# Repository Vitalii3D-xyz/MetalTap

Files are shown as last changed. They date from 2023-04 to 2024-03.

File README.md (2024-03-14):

# MetalTap aka CNC Voron Tap
Drop in replacement for original Voron Tap designed especially for CNC milling. Works with all the same parts as original version.

# Where to buy
- **Worldwide Etsy Shop**: https://www.etsy.com/listing/1446827040/metal-tap-for-voron-cnc-voron-tap
- **EU lab4450**: https://lab4450.com/product/voron-cnc-tap-by-vitalii/
- **EU 3dptronics**: https://www.3dptronics.com/electronics/80-voron-cnc-tap-kit-by-vitalii.html

example of work

# BOM
- 8 BHCS M3x4
- 8 BHCS M3x6
- 1 BHCS M3x10
- 2 FHCS M3x4
- 2 6x3mm N52 disc magnet, get N52m or N52s if you plan to print in high temperature chamber as neodymium will loose magnetism forever after 80C
- 7 Mx3x4x5 heat insert

# Support for other optical sensors
[yonkimen](https://github.com/yonkiman) adapter for inexpensive optical endstop

Sensor: https://www.amazon.com/gp/product/B07MFT8NWJ?th=1

Model: https://www.printables.com/model/803495-modified-opto-mount-for-vitalii-tap/

img_0630 copy

## Assembling Instructions For Kit
[Assembling Instructions](https://www.youtube.com/watch?v=gwPNVVCuMag)

## How to attach belts
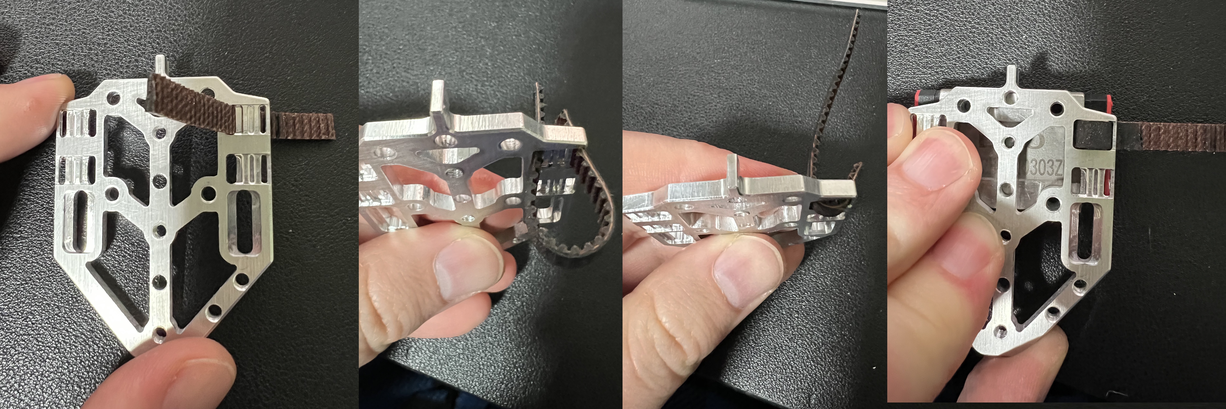
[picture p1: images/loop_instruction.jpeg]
Belts


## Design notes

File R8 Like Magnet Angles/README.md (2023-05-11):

I have tested this version myself, but results are not as good as original version. My Voron 2.4 350 may not be the best machine to test that so leaving to community to test.
# Instrunctions
- Print with Voron parts settings (optional: use Arachne for better letters visibility)
- Insert heat inserts, but make sure that surface is as flat as possible, use sandpaper or exacto knife to remove any
- Parts have L and R letters so attach them accordingly

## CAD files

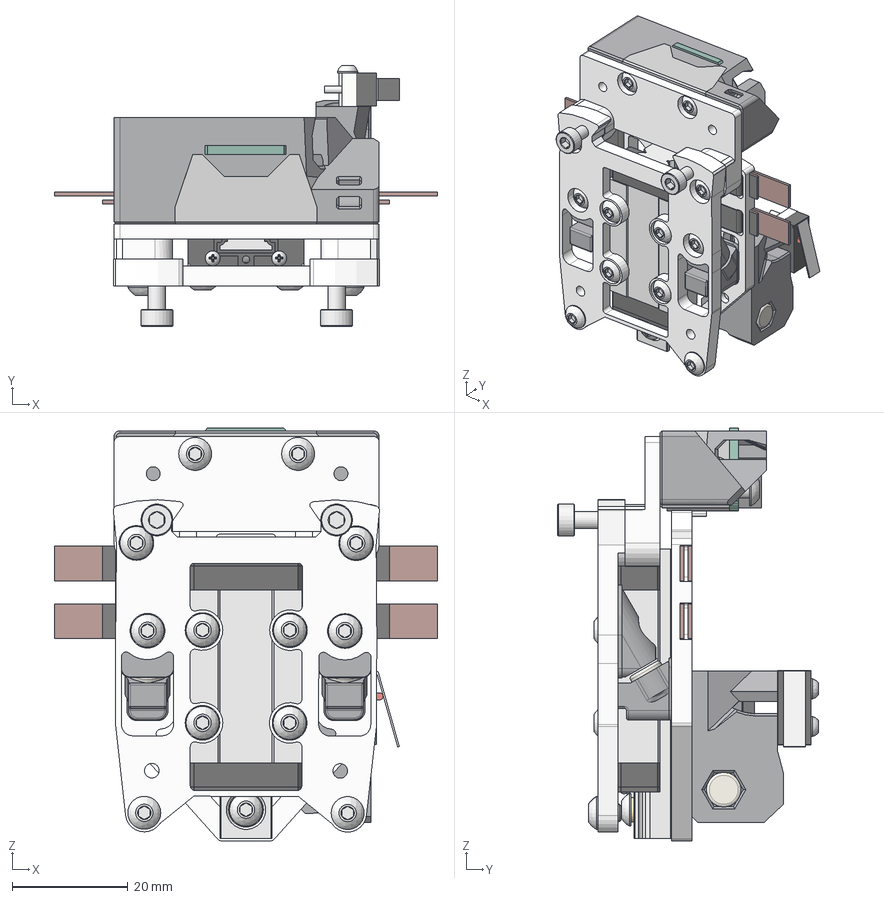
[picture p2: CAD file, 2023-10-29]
CAD/Metal Tap Assembly.step
66.1 x 45.1 x 71.3 mm
MGN9H Carriage
M3x4 BHCS x 8
M3x12 SHCS x 2
M3x6 BHCS x 10
M3x4 FHCS x 2
M3 5x4 Heatset Insert x 7
Carriage Front Screw Holder_1 x 2
6x3mm Magnet x 3
Carriage Center Magnet Holder_1 x 2
M2x10 Self-Tapping Screw x 2
Gates GT2 6mm Belt x 4
OPB990P51Z Optical Sensor
M3x8 BHCS
OptoTap PCB Mount
OptoTap PCB Dummy (1)

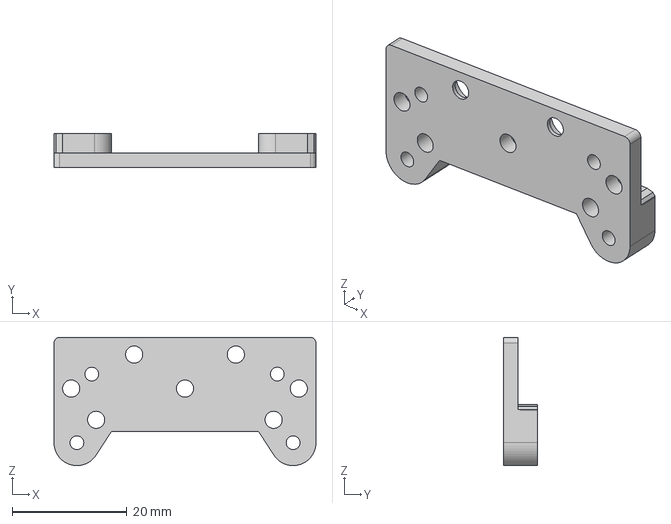
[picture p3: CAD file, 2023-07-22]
CAD/Aluminium Parts/Top Part.step
45.8 x 6.00 x 22.4 mm

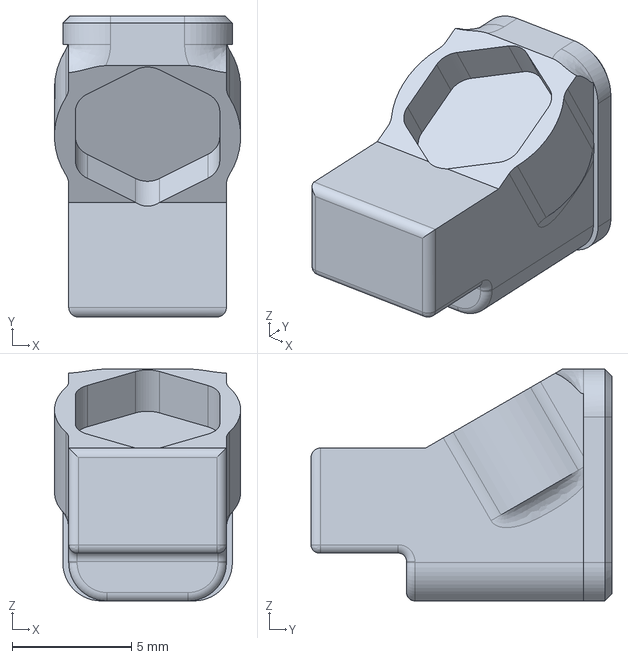
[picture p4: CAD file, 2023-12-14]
CAD/Printed Parts/Carriage Center Magnet Holder.step
7.79 x 12.6 x 9.70 mm

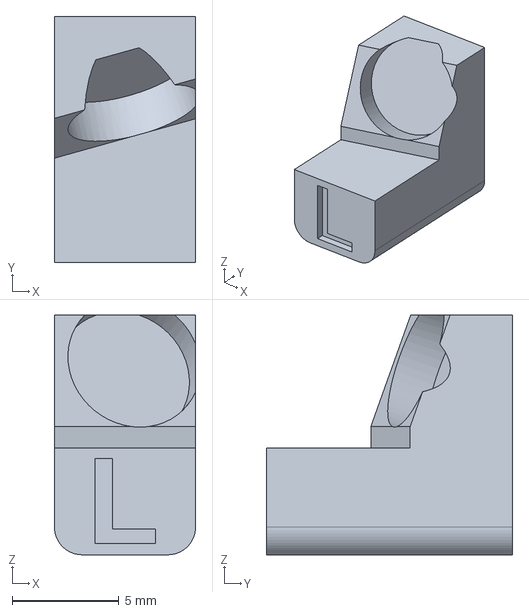
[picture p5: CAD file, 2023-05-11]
R8 Like Magnet Angles/CAD/Carriage Center Magnet Holder L.step
6.60 x 11.5 x 11.2 mm

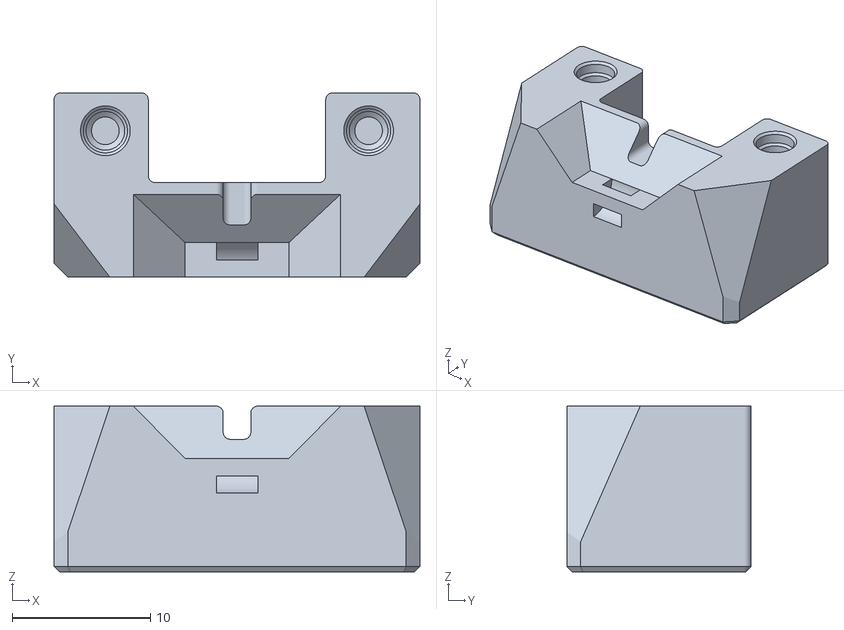
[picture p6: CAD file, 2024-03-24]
STLs/OptoTap_PCB_Mount.stl
26.5 x 13.4 x 12.0

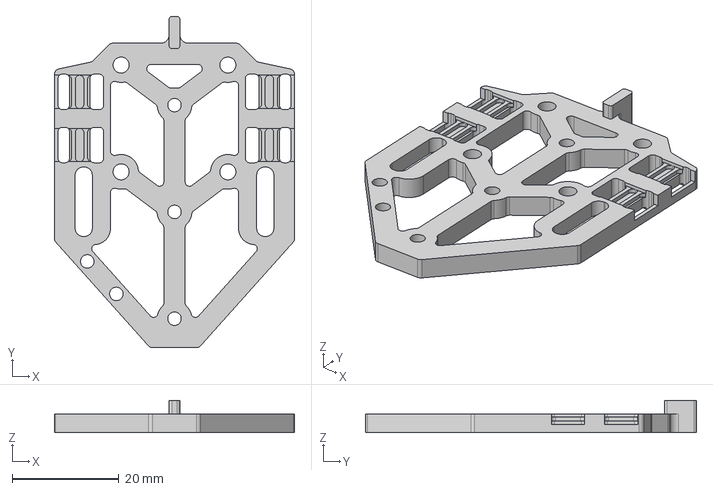
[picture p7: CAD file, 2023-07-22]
CAD/Aluminium Parts/Center Part.step
45.0 x 62.0 x 6.00 mm

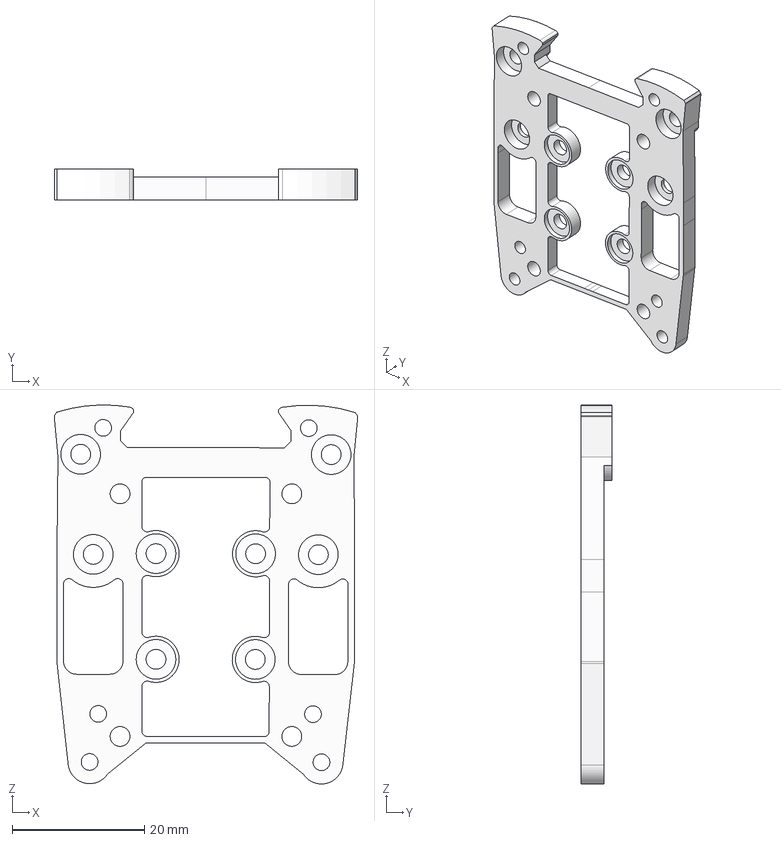
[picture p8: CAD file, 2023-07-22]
CAD/Aluminium Parts/Front Part.step
45.9 x 4.70 x 57.4 mm

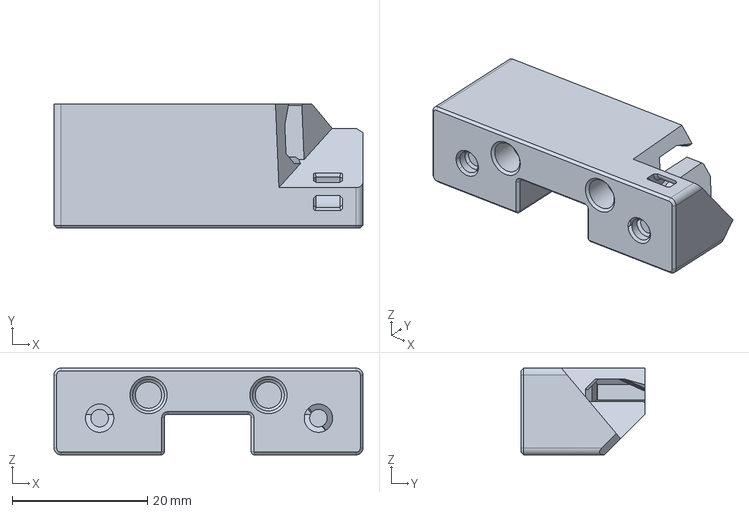
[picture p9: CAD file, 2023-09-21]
CAD/Printed Parts/Wired Optical Sensor Mount.step
45.8 x 18.4 x 12.9 mm

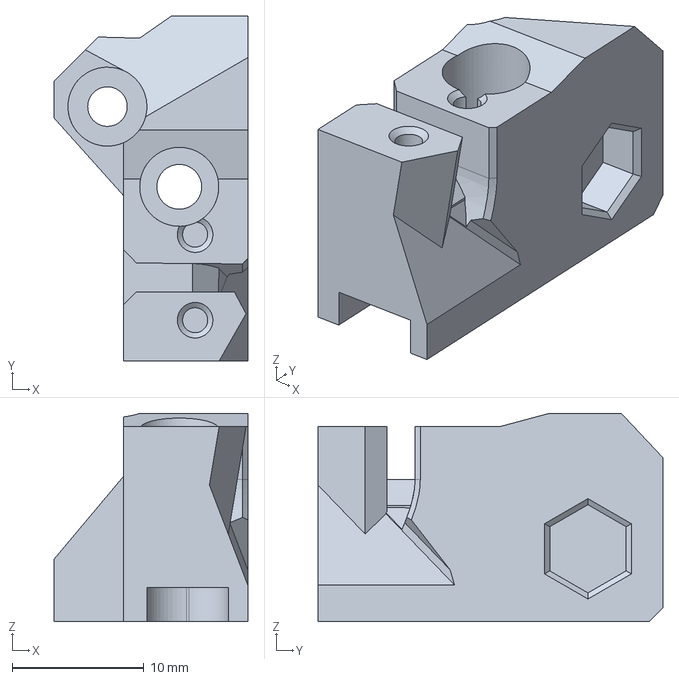
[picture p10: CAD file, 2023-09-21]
CAD/Printed Parts/X Endstop Holder.step
14.7 x 26.2 x 15.8 mm

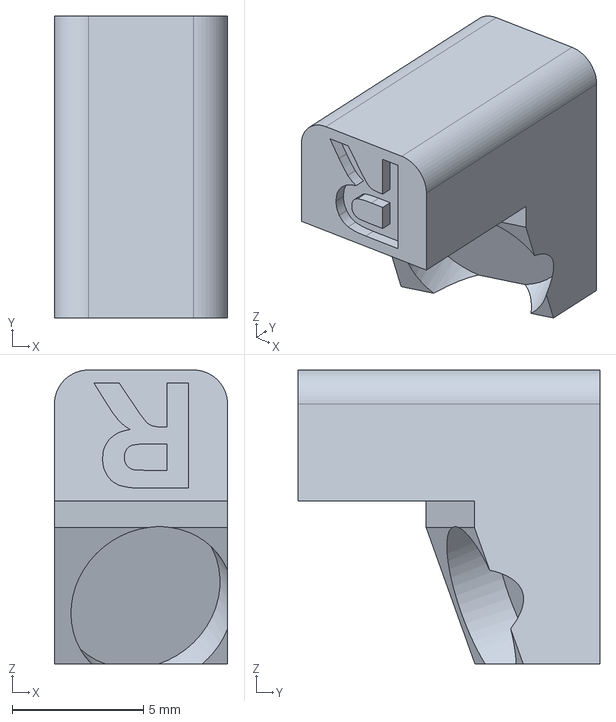
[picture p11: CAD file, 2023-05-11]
R8 Like Magnet Angles/CAD/Carriage Center Magnet Holder R.step
6.60 x 11.5 x 11.2 mm

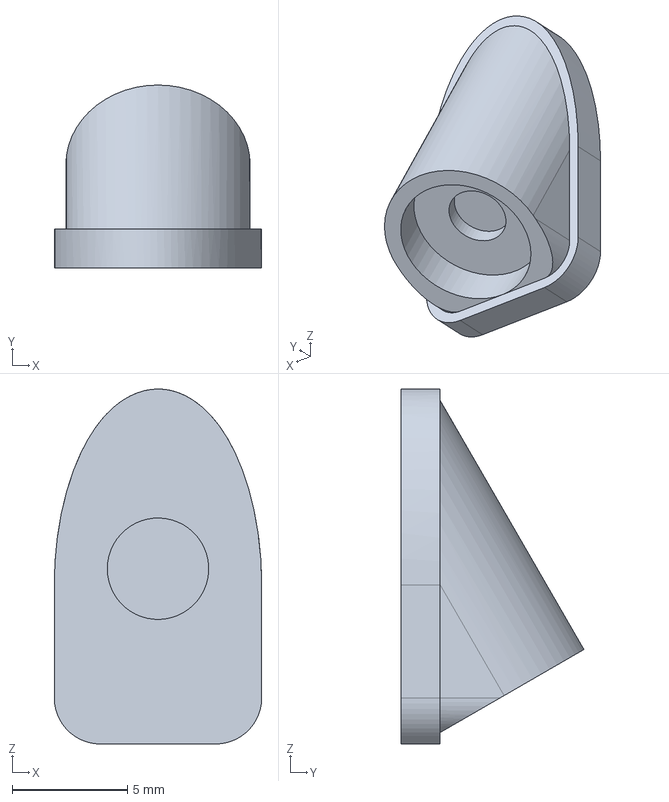
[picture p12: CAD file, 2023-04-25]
CAD/Printed Parts/Carriage Front Magnet Holder.step
9.00 x 7.94 x 15.4 mm

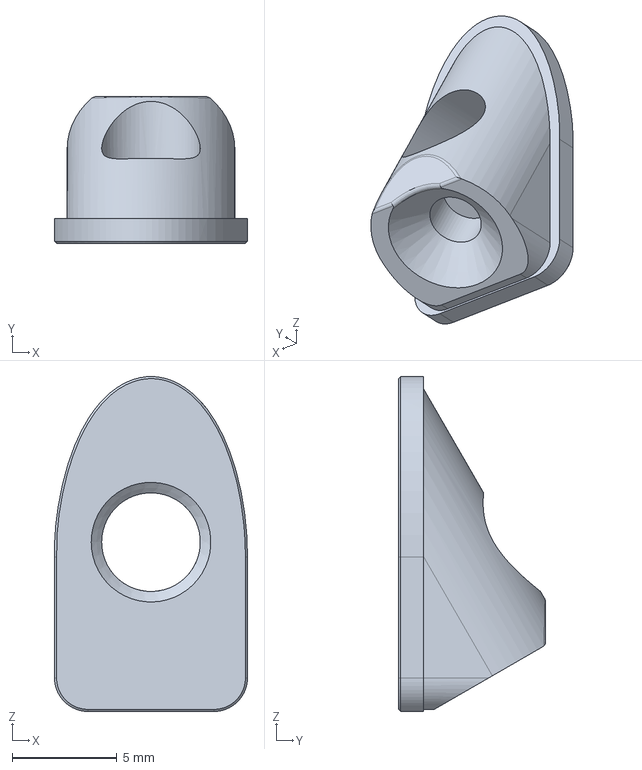
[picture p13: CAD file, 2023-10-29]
CAD/Printed Parts/Carriage Front Screw Holder.step
9.20 x 7.00 x 16.0 mm

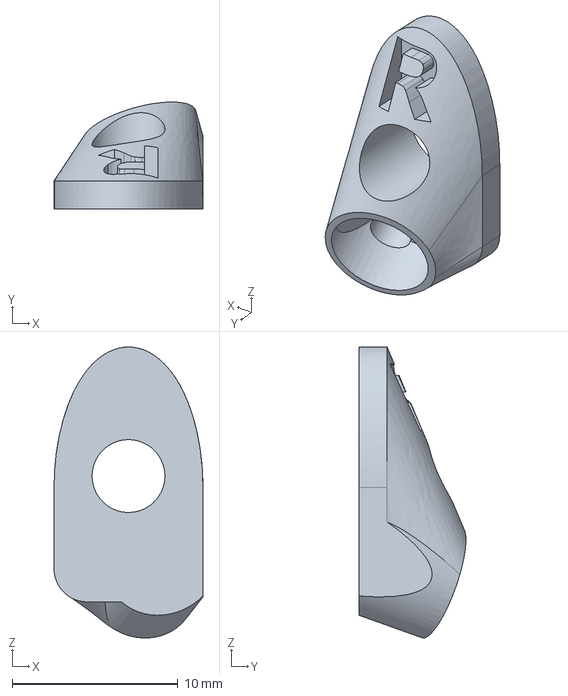
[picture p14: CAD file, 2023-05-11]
R8 Like Magnet Angles/CAD/Carriage Front Bolt Holder R.step
9.00 x 6.46 x 17.6 mm

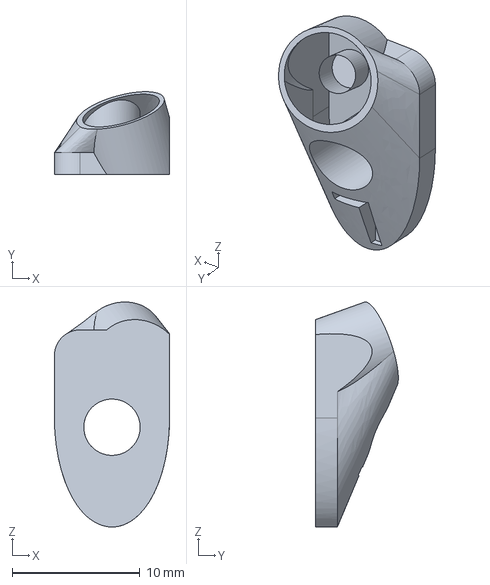
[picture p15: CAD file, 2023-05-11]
R8 Like Magnet Angles/CAD/Carriage Front Bolt Holder L.step
9.00 x 6.46 x 17.6 mm

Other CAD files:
STLs/Carriage Center Magnet Holder x2.stl
STLs/Wired Optical Sensor Mount.stl
STLs/X Endstop Holder.stl
STLs/Carriage Front Magnet Holder x2.stl
R8 Like Magnet Angles/STLs/Carriage Center Magnet Holder L.stl
R8 Like Magnet Angles/STLs/Carriage Center Magnet Holder R.stl
R8 Like Magnet Angles/STLs/Carriage Front Bolt Holder L.stl
R8 Like Magnet Angles/STLs/Carriage Front Bolt Holder R.stl
STLs/Carriage Front Screw Holder x2.stl

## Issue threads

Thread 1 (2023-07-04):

GPL issue? No CAD?

rogerlz, 2023-07-04:
Hey!

I am reaching out regarding the Voron-TAP project and its derivative work in your repository.

As Voron-TAP is released under the GPL (GNU General Public License), it is necessary to publish modifications. However, I could not find the CAD files in your repository. Would you please clarify this matter?

Thanks

Vitalii3D-xyz, 2023-07-05:
Hello rogerlz,

Thanks for the clarification inquiry. This project is indeed compatible with Voron TAP, but it is not derived from it in any shape or form and thus is not required to follow the GNU GPL licensing model.

Saying that I am still planning to release original design into open source community, but so far still looking into the best way of doing that.

samwiseg0, 2023-07-08:
As I can see where you have more than likely made the CAD yourself. The design that you are deriving your CAD from is using GPL thus you need to release your original source files as per the license.

Considering you are using the word "TAP" in your products name that alone supports the case that you used the original work to derive your version. Anyone looking at this product and the original can clearly see that they are _extremely_ similar. Furthermore, you even mention providing printed parts that have the same R8 magnet angles.  Which clearly means you are deriving your design from measurements you have taken from the original work.

Myself and members of the community encourage you to do the right thing in this case and release the files as per the license.

Vitalii3D-xyz, 2023-07-08:
Thanks for feedback @samwiseg0, I am not trying to disagree with you, but would like to understand better what "deriving your CAD from" means in your context. To make my own conclusion I have read GPL 3 again and while it is hard to apply it to CAD (as it was written for software development and operates with different entities) I can see some analogies.
According to GPL 3 derived work is using part of original source in new product, expanding original source or modifying original source. Another very important part is distribution of code.
Good shorter version with examples is available here: https://courses.cs.washington.edu/courses/cse490t/11sp/docs/DerivativeWorksGPL.pdf

Have I used original source in my design or have I modified original source: No
Do I distribute parts of original source: No

I would really like to understand how GPL 3 applies here.
> Considering you are using the word "TAP" in your products name
Is using word TAP automatically makes my work "deriving"? The same for questions about magnets angles. And just in case there are conversation in public Voron discord channel where Olof asks me about R8 angles and gives exact numbers.

samwiseg0, 2023-07-08:
> Have I used original source in my design or have I modified original source: No

I believe this is where the disconnect may be. Even though the original file itself is not being used does not mean that this is not a durative work. Creating your own CAD file does not mean this is not a modification of the original work. "Copying", weather that be by any means of inspecting, the original design and making adaptations to it for it to be CNC is by very nature modifying/adapting the source work.

From the document you linked.
"Under the Copyright Act, a derivative work is defined as "a work based upon one or more preexisting works, such as a translation, musical arrangement, dramatization, fictionalization, ..., or any other form in which a work may be recast, transformed, or adapted. A work consisting of editorial revisions, annotations, elaborations, or other modifications which, as a whole, represent an original work of authorship, is a 'derivative work'."

Example where your product is a direct copy of the original work.
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

An example of a direct parallel in the GPL document you linked that applies to code. If you looked at open source code, typed out portions of it, made modifications, added your own code, and then release that as part of your product. You would then have to release your original source because you derived your new product from code that was part of GPL.

> Do I distribute parts of original source: No

I believe you are taking this literally. Just because the original source (aka CAD file or parts of the CAD file) is not part of your product does not absolve you from following the license. You have based your product off a GPL'ed design and have released it to the public. If you had created this modification/adaptation and _not_ released it to the public then the GPL license could not be applied. Meaning if you used this modified version of TAP for your private use then you would not have to release your modifications.

From the document you linked.
"The critical observation is that the requirement that the GPL be applied to a new work is triggered when 1) a derivative work is created and 2) that derivative work is distributed. "

As an example that _would not_ fall under GPL: <https://github.com/Chaoticlab/CNC-Tap-for-Voron>
It would be difficult to impossible to claim this product as a derivative work since it is fundamentally a different design. Just by looking at this design you can tell it is a stark departure from the original.

Vitalii3D-xyz, 2023-07-08:
> I believe this is where the disconnect may be. Even though the original file itself is not being used does not mean that this is not a derivative work. Creating your own CAD file does not mean this is not a modification of the original work. "Copying", weather that be by any means of inspecting, the original design and making adaptations to it for it to be CNC is by very nature modifying/adapting the source work.

> An example where your product is a direct copy of the original work.

Really?
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

I believe you have misunderstood concept of GPL derived work. That somewhere exist part that is used the same doesn't mean I have used it is cad and doesn't mean I have copy-pasted anything. It is your assumption and I don't like you are making me guilty. From your example please take a look to the comparisons of parts pointed on your picture. Also negative for GT2 belts going to be the same.

> An example of a direct parallel in the GPL document you linked that applies to code. If you looked at open source code, typed out portions of it, made modifications, added your own code, and then release that as part of your product. You would then have to release your original source because you derived your new product from code that was part of GPL.

Again, I didn't used original source (CAD file), I didn't modify it, I didn't improve it. If you can recreate functionality of any GPL protected source it is not violation unless you modify or take parts of original code and it is exactly my scenario.
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
Vitalii3D-xyz, 2023-07-08:
> I'd say so, given that your image is from the back and Sam's image is from the front. No, on the original design, the belt doesn't pass all the way through to the back. However, even in your image, it's clear that the distance that the belt overlaps with the carriage is near identical to the original design.

It is quite possible they are similar, but not the same unless it is some luck as I haven't even try to do that and picked random integer. Just in case for future discussion this is picture of another side:
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

> You don't need to use the CAD to derive measurements, angles, or other geometry. Reverse engineering is an excellent example. If I take a knob for my stove, measure every way I can and then reproduce it in CAD, does that make me the original author of the design? No. I derived my design from the original knob. Albeit this is an extreme example of derivation, the same can still be seen in your design.

> We are imploring you to abide by the GPL3 License as your work clearly falls under it.

If last was true than I would not spend a minute in this discussion and would open source everything under GPL, as I am doing on my Printables account. So far it seems like it is free interpretation of what "derivative work" may be. In software, reverse engineering as disassembling code would be considered as GPL. While re-implementing binary search is not, even if API would be identical to some GPL library, unless sources of that library was used for creating new library.

I would more insist on https://en.wikipedia.org/wiki/Clean_room_design case here.

MasturMynd, 2023-07-08:
> This project is clearly made to help the community, to give everyone access to high-quality well-designed parts. If you don't see that that's on you

Except releasing the CAD and abiding by GPL3 would help the community more by making the design more available to others.

I'm just gonna leave this here and be done with it:
https://discord.com/channels/460117602945990666/1041007230239125574/1102774158749859880

Derivative work is admitted and compliance with GPL3 was accepted. Not sure what changed between then and now.

Vitalii3D-xyz, 2023-07-08:
> Derivative work is admitted and compliance with GPL3 was accepted. Not sure what changed between then and now.

No, I don't see it ever been admitted or GPL3 was accepted. Can you please quote that part?

I agree that I have agreed on release sources, the same was as my first reply on this thread.

MasturMynd, 2023-07-08:
> Can you please quote that part?

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

> I am personally feel offended by this statement. What are "easy money" here?

The only reason to release the design under a license where other people can make it for themselves but not sell it would be to ensure that you're the only one selling them. This is the exact opposite of what the Voron community stands for.

You'll have to excuse me if this came across as crass. That entire message was written at 7am and sleep was eluding me. No offense meant, as I was trying to outline that selling one off designs based on the work of the Voron team wouldn't be lucrative.

Vitalii3D-xyz, 2023-07-08:
@MasturMynd @rogerlz @samwiseg0  @Crawlerin-SA  I believe that this is unlikely than some people become interested in this issue in such short period of time. If you have chat or discord channel where you cooperate then can you please add me so we can discuss it in realtime and be more efficient?

Vitalii3D-xyz, 2023-07-08:
@MasturMynd I strongly disagree that quoted message is accepting GPL3 or admitted derived work. I read GPL3 couple of times, have tried to find examples for CAD or hardware in general and figured out that conversation in discord was misleading and I didn't break any single rule of GPL 3. So as I said "I am not going to break the rules"

Crawlerin-SA, 2023-07-09:
> @MasturMynd @rogerlz @samwiseg0 @Crawlerin-SA I believe that this is unlikely that some people become interested in this issue in such short period of time. If you have chat or discord channel where you cooperate then can you please add me so we can discuss it in realtime and be more efficient?

Hello, best course of action would be opening Engineering ticket - the button is in #request_help channel. Then it can be discussed with Engineering directly, including Badnoob, and pull other people in as necessary.

Vitalii3D-xyz, 2023-07-22:
I have spent a lot of time discussing this issue with badnoob in discord chat. He considered me that accepting GPLv3 is the only way to move forward. I will provide cad files and GPLv3 license within a day.

Vitalii3D-xyz, 2023-07-22:
25% discount until 29th of Jul for everyone :)
https://www.etsy.com/shop/Vitalii3D?coupon=GPL3TOBE

Closed 2023-07-22.

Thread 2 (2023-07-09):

Printed Part Insert Size?

Morfesto, 2023-07-09:
Hello, I printed the following parts but the holes where the threaded inserts go in appear to be too small.

Opto Tap Adapter.stl
Carriege Front Magnet Holder.stl
Carriege Center Magnet Holder.stl

Is it supposed to be something other than an M3 threaded inserts?

Vitalii3D-xyz, 2023-07-09:
I use default heat inserts from Voron BOM. They are little bit tight fit, but feel free to increase size in CAD file.
When bought from my shop you receive all printed parts preassembled, so you may want to leave feedback for shop where you got your aluminium part :)

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

Morfesto, 2023-07-09:
I'm using the same inserts, and all my other holes line up perfect, odd.

Vitalii3D-xyz, 2023-07-09:
Closing

Closed 2023-07-09.

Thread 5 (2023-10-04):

Carriage front magnet holders

Pyromuffin, 2023-10-04:
Hi, the voron tap R8 errata suggests that it's possible to use magnets on the carriage front as well as on the carriage center. It looks like magnets won't fit in the printed screw holders in this design. Would it be possible to add a version that can hold magnets? Or have you tested this and found that it doesn't work for some reason?

Thanks!

Vitalii3D-xyz, 2023-10-04:
Hello @Pyromuffin, as I understand you are trying to run 4 magnets version. I will bring back that option soon, but with rigidity of aluminium 4 magnets version has very strong force and can scratch build plate. I will try to get it ready today

kyleisah, 2023-10-09:
@Vitalii3D-xyz just now seeing a must have accidentally removed the magnet parts when I did the CAD updates. Sorry about that!

Vitalii3D-xyz, 2023-10-09:
4 magnets version is back! Closing this issue

Closed 2023-10-09.

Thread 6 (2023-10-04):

CNC Tap rigidity

BigDaddyV123, 2023-10-04:
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

The issue I am seeing with the Vitalii CNC tap is a common issue around different CNC TAPS. This issue is a lack of rigidity in relation to rotational movement Rx, and Ry. This rotational movement shows up as a Z movement in the toolhead. As stated in the picture plastic tap takes care of this issue with the two screws through the Linear rail attached tap side. Vitalii tap may be able to take care of this movement by created two ribs in the x-direction on the the tap linear rail side which extend vertially along the toolhead mounting side.

Vitalii3D-xyz, 2023-10-05:
Thank you for your analysis!  I trust your results, but the same time it is really hard to think that 2 bolts will add rigidity that MGN rail doesn't have. I have early prototypes that weight more but are much more rigid, if you are interested then I can send them to you to confirm if results are related to rigidity issue.
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

The-Original-Reth, 2023-10-05:
Maybe lack of rigidity is not the right word. And, my conclusion on any potential fix from the data could be completely off. However, I do believe there is an Rx rotation.

I can do further testing. later. I have ordered a second 50mm linear rail for testing purposes

The-Original-Reth, 2023-10-09:
[Vitalii Tap Testing.pdf](https://github.com/Vitalii3D-xyz/MetalTap/files/12851187/Vitalii.Tap.Testing.pdf)

This is the results of my testing. Please feel free to message me if you have any questions

chasebolt, 2023-11-18:
Curious to see more testing around this. Very interesting test results @The-Original-Reth.

The-Original-Reth, 2023-11-18:
[Different Tap Testing.pdf](https://github.com/Vitalii3D-xyz/MetalTap/files/13401137/Different.Tap.Testing.pdf)
This is all the testing I have done with TAP

Ni2Be, 2024-01-17:
I also did some testing with a light weight gantry installed. With the R8 I had a weird PSD that was pretty low but couldn't really be compensated with any function (maybe an unlucky interplay with the light weight gantry - before the light weight it looked more normal).
With the CNC it looks all normal:
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

@The-Original-Reth very interesting analysis, did the strange small peaks get away after replacing the bearings? I once had a super small crack in the left plastic part of the gantry that caused a similar graph.

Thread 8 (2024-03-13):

Not an issue but not sure how to contact you...

yonkiman, 2024-03-13:
(Sorry, I'm not very good with github...)

I modified your Wired Optical Sensor Mount.stl to support [these sensors](https://www.amazon.com/gp/product/B07MFT8NWJ).  I put it on Printables (with the f3d file) [here](https://www.printables.com/model/803495-modified-opto-mount-for-vitalii-tap).

You can add it to your repo if you'd like, you can tell me to take it down, whatever.  Just wanted to let you know.

And also want to let you know that I really like your TAP - I've bought two of them and they're working much better than my plastic ones ever did.

Fred (fred@yonkitime.com)

Vitalii3D-xyz, 2024-03-14:
Thank you Fred! It is amazing addition!
I have added link to your model in README

yonkiman, 2024-03-14:
Happy to contribute!  Feel free to add it to your repository if you want.

On Wed, Mar 13, 2024 at 5:50 PM Vitalii3D-xyz ***@***.***>
wrote:

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

Closed 2024-03-14.

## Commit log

2023-04-24 Added STL files
    [Carriege Center Magnet Holder x2.stl, Endstop.stl, Front Part Bolt Holder x2.stl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]
2023-04-24 Create Opto Tap Mount.stl
    [Opto Tap Mount.stl]
2023-04-25 Updated CAD and STL files
    [Carriege Center Magnet Holder x2.stl, Carriege Center Magnet Holder.step, Carriege Center Magnet Holder.stl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]
2023-05-11 R8 like magnet angles
    [Carriege Center Magnet Holder L.step, Carriege Center Magnet Holder L.stl, Carriege Center Magnet Holder R.step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]
2023-07-22 Adding step files for design
    [Center Part.step, Front Part.step, Top Part.step]
2023-08-13 Center magnet holder update
    Changed magnet hole to octagonal shape and widened sides to add strength.
    [Carriege Center Magnet Holder.step, Carriege Center Magnet Holder.stl]
2023-08-16 Renaming
    carriege -> carriage
    [Carriage Center Magnet Holder L.step, Carriage Center Magnet Holder L.stl, Carriage Center Magnet Holder R.step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]
2023-08-19 Update README.md
    Added link to assembling instructions
2023-09-17 Update to repo
    - Printed parts have been adjusted for easier printing and assembly.
    - Added a wired sensor mount with strain relief for those using a wired optical sensor rather than the OptoTap PCB.
    - Added a complete assembly of the Metal Tap probe.
    [Carriage Center Magnet Holder x2.stl, Carriage Center Magnet Holder.step, Carriage Center Magnet Holder.stl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]
2023-09-19 Adjustment of magnet clearances
    [Carriage Center Magnet Holder x2.stl, Carriage Center Magnet Holder.step, Metal Tap Assembly.step]
2023-10-08 Restore 4 magnets version
    Magnet holder for front part was lost in the latest update, restoring it.
    [Carriage Front Magnet Holder.step, Carriage Front Magnet Holder.stl]
2023-10-15 Updating OptoTap PCB Mount
    - Mount depth decreased by 1 mm
    - PCB mount holes moved down by 0.6mm
    Addressing next issues:
    - At least 2 people reported that in current design OptoTap PCB drags with gantry chain.
    - Couple of people reported that OptoTap has very short travel until it is triggered. Optical sensor moved little bit down now to increase length of triggering.
    [Metal Tap Assembly.step, OptoTap PCB Mount.step, OptoTap PCB Mount.stl]
2023-10-29 Updated printed parts with zero play versions
    This change address next issues:
    - printed parts have some play in aluminium parts pockets because of ABS shrinkage. Now that is compensated and makes assembly easier. Potentially may improve IS results
    - Increased range of motion for carriage allowing to move it lower
    - Bolt holders are adjusted so can be used together with 2mm belt holder clamps
    [Carriage Center Magnet Holder x2.stl, Carriage Center Magnet Holder.step, Carriage Front Magnet Holder x2.stl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]
2023-12-14 9mm belt support
    Magnet holder parts are updated to be compatible with 9mm belt version
    [Carriage Center Magnet Holder x2.stl, Carriage Center Magnet Holder.step]
2024-02-24 increase clearance under the pcb for OptoTap 2.4.1 from Lab4450.com
    [OptoTap PCB Mount.step, OptoTap PCB Mount.stl]
2024-03-23 Update PCB Mount with a ZipTie Hole for V1 Taps.
    [OptoTap_PCB_Mount.stl]
